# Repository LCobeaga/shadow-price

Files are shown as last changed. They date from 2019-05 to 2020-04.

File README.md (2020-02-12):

Shadow Price
=====

###### Shadow Price is the culmination of many years of CADing, which I had to learn along the way, and Coding, most of which I was taught by @mochoy. It uses brushless motors for the flywheels, a solenoid pusher, and has an integrated IR beam based ammo counter. The shell is based off of the stock weapon model for an auto rifle in the video game Destiny, and my personal blaster is painted like Shadow Price. 

### The STLs for all components are not inhenretly in the correct priting orientation, however there are large flat areas on all parts so use your best judgement when printing and print on these faces

### All minor changes to this document will be dated and placed at the bottom, major changes will be noted at the top here

### Note: This version uses tighter tolerances on all print surfaces. You will likely have to file the removeable components to get them to slide past each other.

## Parts List

For this Blaster you will need:

### Hardware
- 18 Regular Nerf screws (10mm long)
- 10 Small Nerf screws (5mm long)
- two small washers that will not slide over the main screw heads (or switch two of the small screws for something like the washer screws that are used on Stryfe mag releases)
- A small extension spring for the trigger
- A small compression spring for the magazine release (pen spring works)
- Optional: 
  - An 8-32 or M5 machine screw and nut (to hold up butt plate)

### Ammo Counter Electronics
- An Arduino Pro Mini 5V/16MHz 
- A small solderable breadboard
- two .56" 7 segment displays 
- two resistors (based on the color of your display) 
- two 7 segment decoders (make sure they are the same type as your displays)
- two 5mm breadboard compatible momentary push buttons
- A 3mm [IR break beam](https://www.adafruit.com/product/2167)
- A small [limit switch](https://www.allelectronics.com/item/sms-371/spdt-mini-snap-action-switch-w/sim-roller-lever/1.html)
- 22 gauge wire
- Heat shrink 
- Optional: 
  - Multiple colors of wire (to differentiate each button)
  - Bread board jumpers (for creating protoboard)
  - Crimp connectors (for power and ground from ESC-BEC)

__Firing System Electronics__
- An Arduino Pro Mini 5v/16MHz 
- A 10K Ohm [potentiometer](https://www.amazon.com/PoiLee-Potentiometer-Linear-WH148-Shaft/dp/B07BW8JBC8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)
- A medium sized [limit switch](https://www.allelectronics.com/item/sms-219/spdt-mini-snap-action-switch-w/roller-lever/1.html)
- A male battery connector of your prefrence 
- Two ESCs with BEC that are rated up to 3s and have a high enough amperage for your motors
- Two 2204-2300Kv brushless motors (currently working on adding support for 1806 sized motors as well)
- A 35mm stroke 12v electric solenoid 
- A 1N540x Rectifier Diode 
- A IRLB3034PBF MOSFET 
- A 10K Ohm resistor 
- 22 gauge wire
- 16 gauge wire
- heat shrink 
- Optional: 
  - 5mm bullet connectors (for removeable ESCs and easy polarity switching)
  - Crimp connectors (for power from ESC-BEC and to keep small control cables organized)
  - Suild's [MOSFET board 2](https://suild.com/shop/0) (as a replacement for all the MOSFET components)
  
## Software

### Firing Code

To Start, you will need to download the [JC Button Library](https://github.com/JChristensen/JC_Button) by Jack Christensen. 
If you dont know how to download a library to your Arduino IDE [this is a good guide](https://www.digikey.com/en/maker/blogs/2018/how-to-install-arduino-libraries) that I used, just scroll about half way down and there are two mehtods to download the library. 
There are only two areas in the code you should ever realistically need to change, the pinout and revSequence. 
The pinout is simple:
```
#define TRIGGER_PIN 9
#define MOTOR_PIN 10
#define ACTUATOR_PIN 11
#define POT_PIN 1
#define FIRE_MODE_PIN 7
```
- TRIGGER_PIN is for the trigger microswitch.
- MOTOR_PIN is for ***both*** of the signal wires from the ESCs, so make sure you splice the wires together at some point.
- ACTUATOR_PIN is for the signal wire coming off the solenoid MOSFET, in the case of the MOSFET board 2 from Suild it would be a wire coming off the gate pin.
- POT_PIN is for the 10K Ohm potentiometer signal pin, the wire that comes from the middle tab.
- FIRE_MODE_PIN is for an unutilized two position switch that would change between full auto and three round burst. While the code is written for this, there is no mounting geometry in the 3D prints, so you would have to download the .step file in the prints folder and model it in yourself.

The other area of code you might need to change is:
```
void revSequence(){
  flywheelESC.writeMicroseconds(1860);                
  delay(map(analogRead(POT_PIN), 0, 1023, 150, 50));    
  flywheelESC.writeMicroseconds(map(map(analogRead(POT_PIN), 0, 1023, 0, 100), 0, 100, 1250, 1650));
  delay(70);
}
```
In this function you might have to change the delays based on your motors' spin up time. In the first delay, the only values you might need to change are the 150 and 50, which determine how long you need the motors to accelerate for. 
Effectively, the motors accelerate the greatest when an immediate command to full speed is sent. 
What this line of code is doing is using that concept to put the motors at max acceleration for longer when the potentiometer is set to a low speed and accelerate for less time when at the optimal speed. 
Without this line of code the spin up times for all motor speeds would be significantly greater, so change these values only if your first dart fires significantly harder than the rest of your darts when holding the trigger.

The second delay at the end of the function is less complicated, and the only value you might need to change is the 70. 
Once the motor has been told the desired speed (from the previous line of code) it needs a moment to reach it, so the delay is just waiting for the motor to reach that speed, so if your blaster constantly jams when firing the first shot increase this delay, and if you feel like the first dart takes an eternity to fire decrease the delay. 
If you are going to play with this number I suggest you increase or degrease by units of 5 until you reach the minimum delay where your blaster wont jam. 

If you use a different ESC than the 12A AFRO that I use, the min and max speed in microseconds (1860) might be different, and since you will use different motors than the 2204-2300KV Turnigy Multistar Elites (because they are discontinued) the minimum firing and optimal speeds in microseconds (1250 & 1650) will be different. 

To find the max and min speeds in microseconds you will have to refer to the instruction manual that is associated with your ESC, or just test values until you find the threshold value where the motors begin to spin (the minimum microseconds) and find the threshold value where the motor speed does not seem to contimue to increase. 
Once you find these values just ctrl+F in the arduino IDE and switch out every 1060 & 1064 for your new minimum value and switch out every 1860 & 1864 for yor new maximum value (including in the setup code). 
Make sure all of these test you conduct inside the assembled blaster, since it is dependent on the solenoid firing 

To find the minimum firing and optimal speeds you will have to rely solely on testing. 
For minimum firing value, increase from the minimum value in incriments of 10 until you can fire 10 shots full auto without jamming. 
For optimal value, degrease from max in incriments of 10 until the FPS of the dart begins to drop, and you'll need a chronograph for this test (or just look at range with measuring tape, but that will take longer and require more walking). 
These tests can be conducted outside of the blaster, with you manually feeding the darts into the flywheel cage, but it's better if you conduct them inside the blaster since the results will be more realistic. 

### Ammo Counter Code

I will preface this section by saying that this ammo counter is not exlusive to Shadow Price, if you can find some other low current 5v power source to plug it into it will work completely independent. 
The amount it can count up to is also expandable, so if you want to make an ammo counter for your backpack fed blaster feel free to use this design, good luck with counting how many balls you put in at the beginning though. 

Just like before the pinout is relatively simple
```
#define DIG_ONE_A 2
#define DIG_ONE_B 3
#define DIG_ONE_C 4
#define DIG_ONE_D 5
#define DIG_TWO_A 6
#define DIG_TWO_B 7
#define DIG_TWO_C 8
#define DIG_TWO_D 9

#define IR_BEAM 14
#define MAG_SIZE_UP 10
#define MAG_SIZE_DOWN 11
#define MAG_SENSOR 12
```
- DIG_ONE_A-B and DIG_TWO_A-B are the A-B signal pins on the 7 segment decoders, ONE and TWO being for the tens and ones digits, respectively. 
- IR_BEAM is for the signal pin of the IR break beam sensor. 
- MAG_SIZE_UP is for the button that increases the magazine value. 
- MAG_SIZE_DOWN is for the button that decreases the magazine value. 
- MAG_SENSOR is for the limit switch that goes inside the magazine well. 

If you are using this ammo counter for Shadow Price or any other under-100-dart-capacity blaster the only other variables you might change are:
```
int BASEmag  = 17;
int MAXmag   = 35;
```
- BASEmag is the value the ammo counter will show on boot up.
You'll be able to change this value using the up and down buttons, so it doesn't really matter what this value is as long as it's less than the MAXmag value; I like putting it as the capacity of my first magazine in my loadout. 
- MAXmag is the greatest value the ammo counter will display, and the value at which it switches back to 0 if you keep hitting the MAG_SIZE_UP button. 
Make this value the capacity of your largest magazine you would put into the blaster; In my case the largest magazine I own is the 35 round drum. 

Now, if you want to expand this ammo counter to three digits (999 rounds max) or four digits (9999 rounds max) its pretty simple. 
1. Repeat the code in ```void func()``` that displays the ones position for every added digit (I suggest you put it at the end of the function to keep the code organized). 
2. Replace the variable in the ```digitalWrite();``` on your repeated section with the new pinout for your extra digit(s). 
3. Replace the conditions in the DIG_ONE display code with your new highest values (e.g. replace the 10,20,30, etc. with 100,200,300, etc)
4. In decending order, update the conditions for the new digits (e.g. replace the %10 == 1,2,3 etc with %100 == 10,20,30 for digit two, and then leave the conditions alone for the last digit). 
5. Update the BASEmag and MAXmag to values that better reflect your new ammo capacity.

If this didnt make sense feel free ask via reddit (u/Band3rsnach) and I can help, but none of this last bit is required for Shadow Price. 

## Printing and Assembly

### Recomended Printing Orientation

To save time in generating these images I've placed multiple parts on a single print bed. 
I am NOT suggesting you print multiple parts at once unless you are confident in your printer's ability. 
As a general rule, internal features will not need any support, and external features will require supports (if you want the blaster to look pretty). 
A few parts (tail, stock panel left, trigger well left) have extrememly thin surfaces that are for bridging or to reduce supports. 
If you are confident in your printer's ability to bridge use them, if not the surfaces should not cause any problems with supports. 

barrel 1

Depicted: 3X Barrel Tip, Barrel Front, Barrel Middle, Barrel End, 2X Key, Lock

barrel 3

Depicted: Battery Tray

body 1

Depicted: Handle, Knuckle Duster, Left & Right Grill, Bottom Dovetail, Pusher Cover, Solenoid Cover, Top Dovetail, Trigger

body 2

Depicted: Solenoid Mount, Tail, Tail Dovetail, Trigger Well Left & Right

The thin surface circled in red on Trigger Well Left is a built in support, and the Tail has a thin surface for bridging inside it. 

functional

Depicted: Flywheel Smooth, High Crush Flywheel Cage

magwell 1

Depicted : Alignment Bar, Archway, Battery Tray Latch, Bottom Dovetail, Cage Mount, Flywheel Cover, Mag Release Lever, Mag Tooth, Magazine Release, Picatiny Left & Right, Top Dovetail

magwell 2

Depicted: Magwell, Insert

stock

Depicted: 2X Button, 4X Slot, Button Mount, Buttstock, Fin, Left & Right Panel, Stock Main

The part circled in red is the Left Panel, and uses a thin surface for bridging in two areas near each button. 

### Assembly

Now, if like me you are impatient and like to assmeble as you print, I suggest you begin by printing all the parts in the Body and Magwell folders. 
These two folders will make up about 60-70% of your time building Shadow Price since they have a relatively complex assembly that keeps the blaster robust and secure. 
I **highly** suggest you use some form of solvent weld for this blaster instead of an epoxy or superglue, as there are some areas that can take a lot of stress during a fall, and its better to be too secure rather than not. 
For PLA I suggest Weldon 16, for PetG or similar Pet filaments I suggest Weldon 3 or 4 (4 is just more viscous, same formula), and for ABS obviously any form of acetone.
> One cool thing with Weldon 3 or 4 is that it also bonds styrene plastic, so if any part warps (like the Flywheel Cover) you can glue on styrene and it should be super easy to shape and fill gaps. Another good thing about specifically Weldon 3 is it is water thin, so you can use a small spray bottle head (make sure it doesnt disolve in the solvent!) or a brush to cover areas that seem to be cracking. This bonds the layers together like annealing and will make the area stronger (if you can, do this along the top angle of the Cage Mount). You can probably tell at this point that I printed mine in PetG. 

Ok, suggestions over, lets start assembling:

1. Screw into place and glue down Tail Dovetail into tail
step -1

2. Screw into place and glue Insert into Cage Mount

step -2

3. Glue the Cage Mount, Archway, Solenoid Mount, and Tail together in a line. We will call this group the "upper reciever"
step 1

4. Glue and snap the Magwell and Battery Tray Latch together by aligning the circular cutout and snapping in the triangular piece. If you are using a water thin solvent snap the parts together then put a bit of solvent in between the parts.
step 2

5. Glue the Alignment Tab into the Magwell. It should be a tight fit.
step 3

6. Place the Mag Release lever into the Mag tooth and slot both into the back of the Magwell. Make sure the the cutout part of the lever faces away from the magwell, the part of the tooth that sticks out is towards the bottom of the magwell, and that **no glue** gets on any of these parts. 
step 4
step 4-2

These next two steps need to be done pretty quickly if you are not using a water thin solvent, so prepare everything before hand. 
If you are using a water thin solvent, just dont put any solvent in until after all the pieces are locked in place. 

7. Glue and slot Trigger Well Right into the back of the Magwell. This will lock in the magazine lever and tooth so it is critical you align those before gluing this piece on. This collection of pieces we will call the "lower reciever".
step 5

8. Glue, slot, and screw the upper and lower reciever together. Make sure the Alignment Tab is pushed into the back and top of the slot in the Archway, the spike on the front of the Cage Mount is flush with the cut out in the Battery Tray Latch and the screw is in place, the L shaped extrusion is in the corner of the Trigger Well Right, and that the entire top surface of the lower reciever is flush with the bottom of the upper.
step 6

From here on the rest of the parts are mostly cosmetic, however they make up a lot of the length and weight of the blaster.
Make sure they are securely glued and mounted in place or you might get cracks in the shell after painting.

9. Glue and slot the Handle into the bottom of the Trigger Well Right. It should be a secure fit, just make sure you push it as far up as possible. 
step 7

10. Place the small extension spring on to the Magazine Release pin, and insert the pair into the Knuckle Duster. Make sure the spring sits flat on the inside of the Knuckle Duster. I also suggest you paint this component before you put it in since there is no way to get it out. (Optional: add a bit of craft foam to the front of the Magazine Release to make it more comfortable to hit with your middle finger)
step 8

11. Slot the Knuckle Duster assembly into the bottom of the Trigger Well Right and the bottom of the Handle, and align the Magazine Release with the Mag Release Lever, making sure that the system is free to move.
step 9

12. Screw the Knuckle Duster into the bottom of the Handle and glue the top of it into the bottom of the Trigger Well Right and the Magwell. Be careful not to get glue on the release system. 
step 10

13. Glue and slot the Stock onto the back of the Tail. Be sure to get good adhesion both inside and on the two flush surfaces. 
step 11

14. Glue and slot the four Slots into the back of the Stock. Be sure to press them in firmly or the buttplate might be wobbly.
step 12

15. Glue and slot the Right Panel onto the right side of the Stock. Make sure to get good adhesion between the front of the panel and the Tail.
step 13

16. Moving back to the front of the blaster, glue and slot the Top & Bottom Dovetails to the Cage Mount and Battery Tray Latch. Make sure they are flush with the exterior of the blaster. 
step 14

17. Glue and slot Barrel Middle and Barrel Back into place 

step 14b

18. Glue, Slot, and Screw the Barrel assembly into place. 
Make sure it is flush against the Cage Mount both in the front and on the sides.
step 15

The next two steps are for one of the removeable covers, make sure not to glue it into the rest of the blaster.

19. Glue and slot the top and bottom dovetails into the Solenoid Cover
step 17

20. Glue and slot the Trigger Well Left into the bottom of the Solenoid cover. (Optional: glue the two at a slight inward angle so that when screwing into the blaster the panel will always fill the break at the top)
step 18

21. Screw Picatiny Left & Right into the Flywheel Cover and Cage Mount, respectively.
step 19a
step 19b

22. Slot and Glue Grill left & right into the solenoid panel assembly and Solenoid Mount, respectively.
step 20a
step 20b

23. Slot and Glue the three Barrel Tips together.
step 21

Now other than removeable components (Which are screw in) the blaster is fully assembled. 
I suggest that you dont glue the barrel tip assembly into the Barrrel End because its prone to breaking, and make sure that at no point do you glue the Flywheel Cover, Barrel Front, Buttstock, and the Solenoid Cover/Trigger Well Right assembly to the rest of the blaster or you will be unable to insert the internals. 

## Wiring

The blaster can be broken up into two circuits controlled by each of the Arduino Pro Minis and powered by each BEC output. 

This is the diagram for the ammo counter
Ammo_Counter

And this for the firing system
Firing_System

# Updates 

## 10/15/19
2Xkey file was added into the barrel folder. Two of them should be printed along the longest dimention and glued together. Will requre a little less sanding than the regular key, but it will still be a tight fit.

Swapped Left Panel and Stock Main in the stock folder for new versions that make use of a screw and bridging characteristics. No changes to printing orientation. Added another screw in the parts list.

## 10/16/19
Made changes to a majority of body components to improve aesthetics and to remove remnant geometry from older versions. 

Major changes include a block to better attach the Handle to the Trigger Well Right, combining the Solenoid Mount and Top Picatiny to prevent cracking in both parts (as observed in my personal print), and adding a 1 deg angle to the connection between the Trigger Well Left and Solenoid Cover to close shell gaps.

Began to strenghten area around mag release by increasing contact between the Magwell and Knuckle Duster, however no changes have been made to the Magwell so currently the blaster is non printable. 

Updated printing orientation photos and removed assembly step 16 pertaining to the Top Picatiny. 

## 11/24/19
Broke down Barrel Main into two components, Barrel Back and Barrel Middle.

Replaced Barrel end with Barrel Front, now with the new attachment lugs and optimised for bridging. 

## 11/25/19
Filled in gaps between Tail, Solenoid Mount, Solenoid Cover, Trigger Well Right, Magwell, Cage Mount, Flywheel Cover and Archway.

Cut out space in Magwell for the new Knuckle duster, now making the blaster printable again. 

Cut a hole in the top of Cage Mount.

- Created two new parts, Tail Dovetail and Insert.
- Tail Dovetial holds Solenoid Cover from the back and hopefully reduce flexing on Solenoid Mount.
- Insert goes inside of Cage Mount and will hopefully reduce the cracking that occurs in that area.
- Parts list updated to reflect four screws that hold the pieces in place.

## 11/26/19
Increased Insert tolerances. 

Added fillets to the picatiny on Solenoid Mount to reduce the need for supports.

Updated printing and assembly photos to reflect geometry changes. 

NOTE: Since many changes had no effect on assembly, not all photos were switched out, so go by description and use the photos as refrence. 

## 12/11/19
Multiple minor geometry changes as I print another shadow price and issues arise. 

- Pushed back dovetail and increased angle on Handle.
- New female side of dovetail on Trigger Well Left.
- Added screwport between Trigger Well Right and Left.
- Added reinfocement bar to Solenoid Cover to prevent cracking on small upper area.
- Removed extraneous walls in Archway to help with aethetics.
- Minor wall adjustments on Solenoid Mount so it meshes better with Archway and requires less support.

Updated Parts list with extra screw.

## 12/14/19
Redesigned all dovetails connecting the removeable handle cover from the blaster.

- Added new part, Tail Decoration, to prevent the need for a large support tower.
- Added a Dovetail to the side and back of Magwell and Archway. 
- New locations for two of the screws, moved from Trigger Well Left onto Solenoid Cover.
- Removed Top and Bottom Dovetails as they are now extraneous parts.

Created new set of combined parts for larger printers (150mm+ in X or Y).

- Added new parts Trigger Well Left Combined, Trigger Well Right Combined, Handle Combined.
- Moved geometry constraining the magazine release system onto the trigger well pair, should now allow for removeable components.

No changes to assembly order but some steps need to be removed due to dovetail changes.

## 12/16/19
Reinforced Magwell and surrounding parts

 - Added bridge support to Magwell dovetail.
 - Thickened wall on Magwell under the cage.
 - Made the anchor for Battery Tray Latch larger.
 - Removed extra features on inside of Cage Mount, added chamfers to reduce supports and increase strength, added extra screwport at the top of the Back Barrel connection, thickened walls and added bridge supports. 

Minor changes to Solenoid Mount and Cover to reduce required support.

Removed the original trigger well files as the new dovetail geometry was not reflected in their design and made them redundant.
The Knuckle Duster does not reflect the changes on the Trigger Well Combined files, so for now only use Handle Combined.

Cleaned up extraneous surfaces on stock main.

## 2/12/20
Dropped height of Battery Tray so top is planar, makes printing easier.

Increased wall length of Barrel Middle and Front to match Battery Tray.

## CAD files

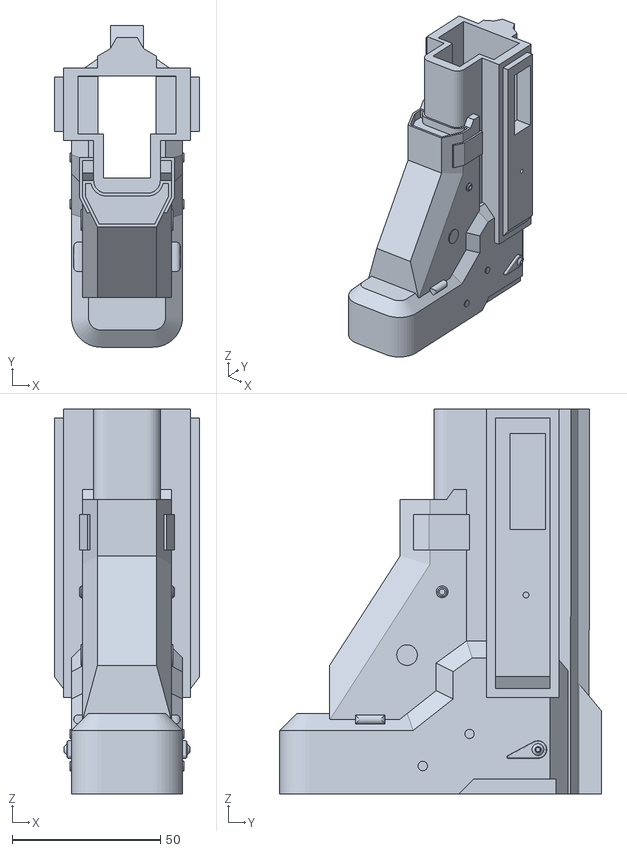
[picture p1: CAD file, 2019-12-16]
prints/stock/stock main.stl
49.0 x 108.6 x 130.0

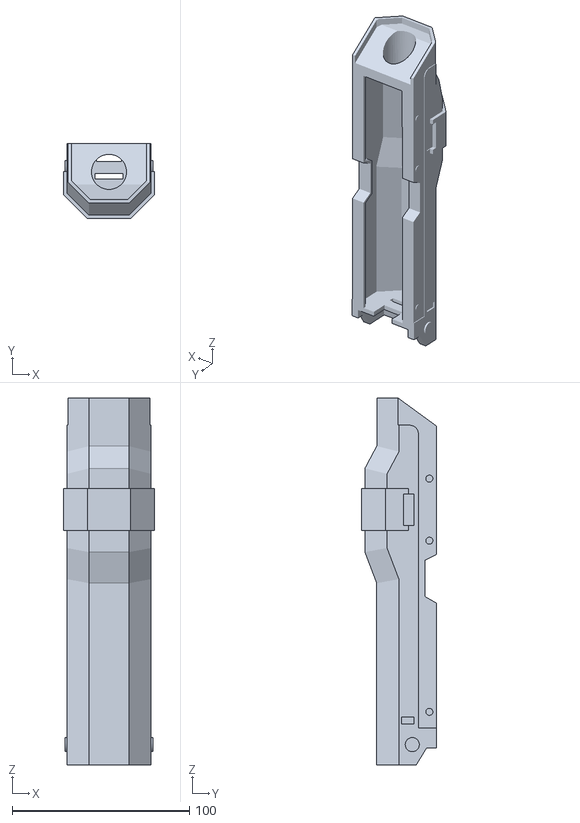
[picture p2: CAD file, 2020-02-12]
prints/barrel/battery tray.stl
51.5 x 42.5 x 206.9

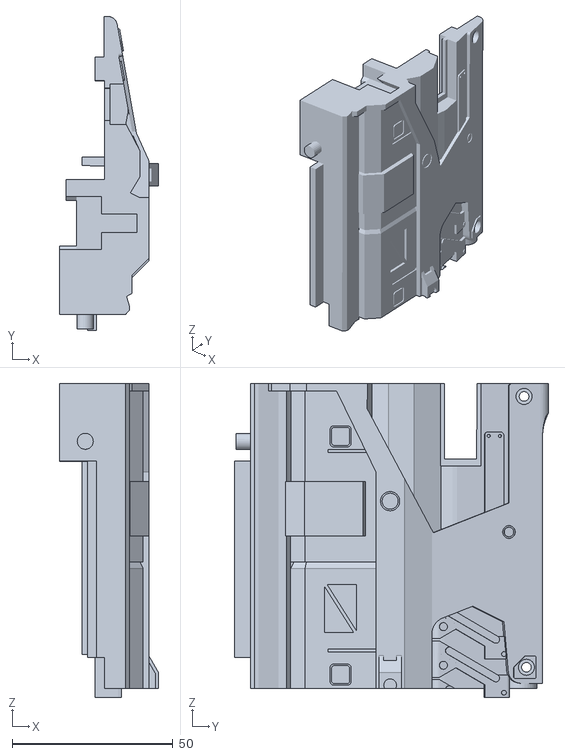
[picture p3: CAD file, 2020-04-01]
prints/body/solenoid cover.stl
30.8 x 97.6 x 97.6

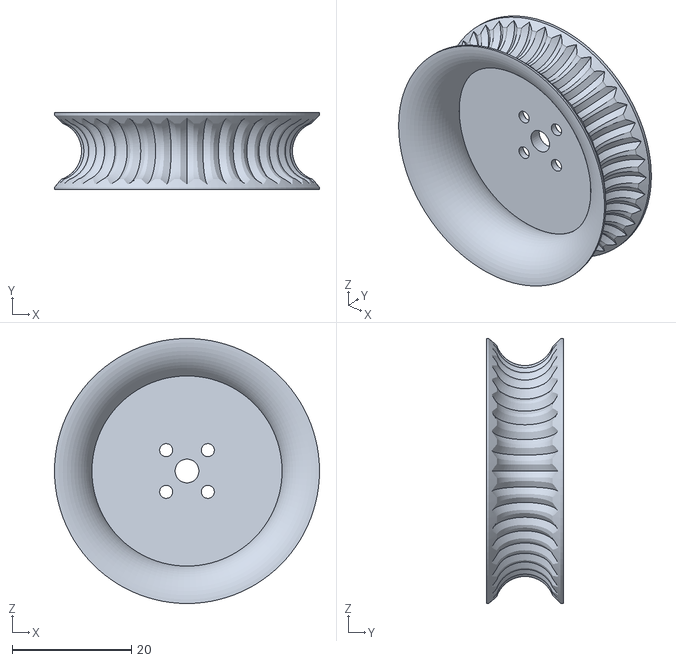
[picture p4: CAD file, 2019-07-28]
prints/functional/current/flywheel vertical lines.stl
44.5 x 13.0 x 44.5

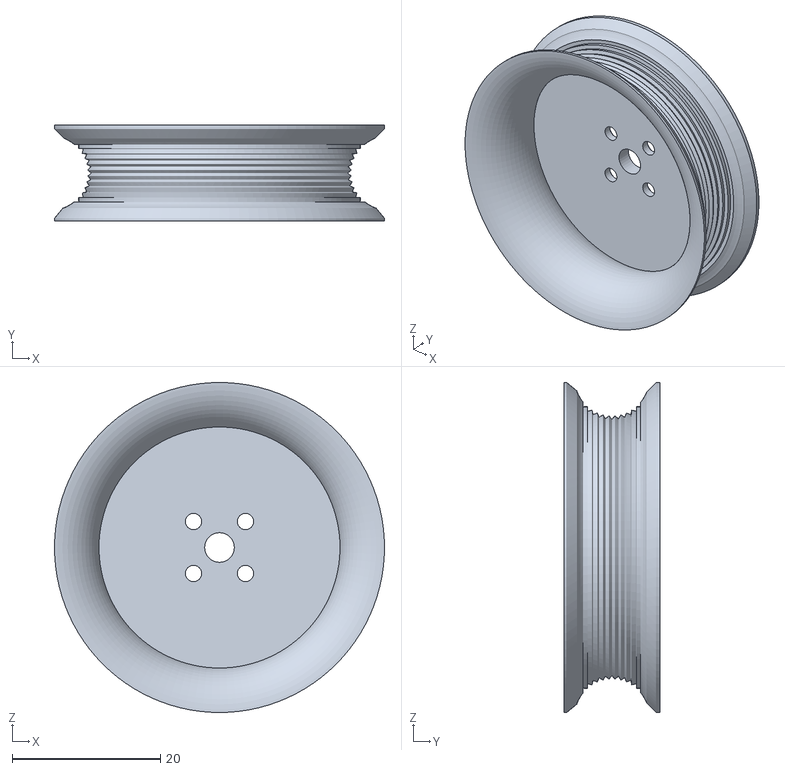
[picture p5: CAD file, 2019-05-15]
prints/functional/flywheel lateral lines deep.stl
44.5 x 13.0 x 44.5

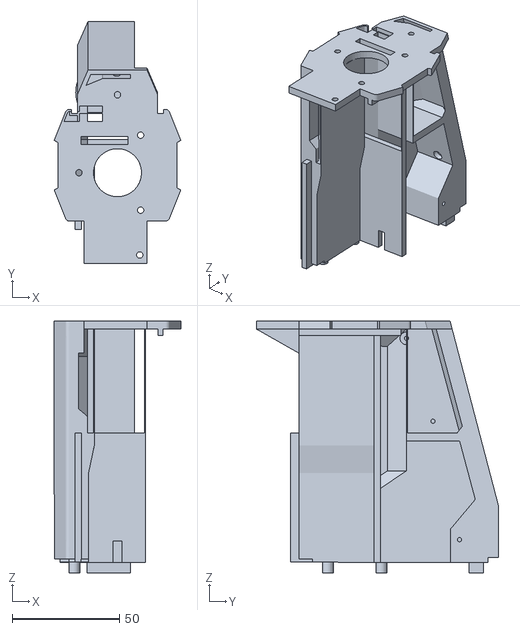
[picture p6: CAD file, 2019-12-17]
prints/magwell/cage mount.stl
59.1 x 113.0 x 117.6

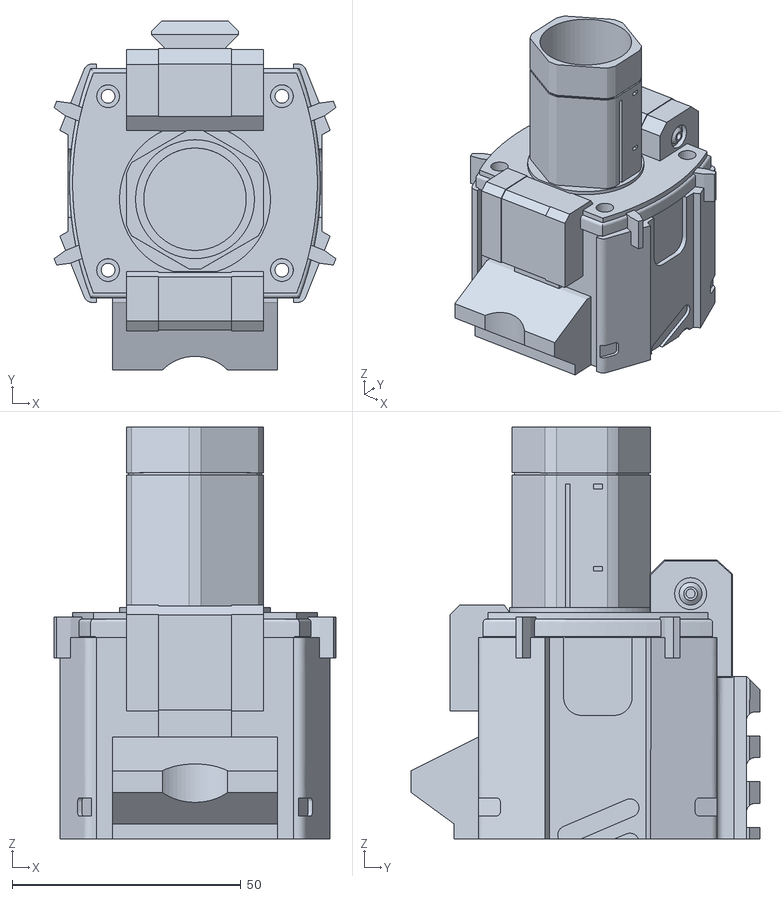
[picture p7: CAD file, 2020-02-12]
prints/barrel/barrel front.stl
61.6 x 76.3 x 90.1

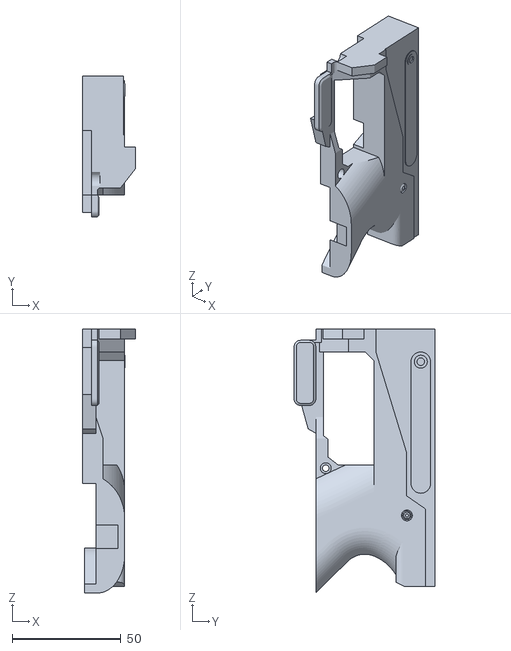
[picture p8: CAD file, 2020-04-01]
prints/body/trigger well left combined.stl
24.5 x 64.8 x 121.4

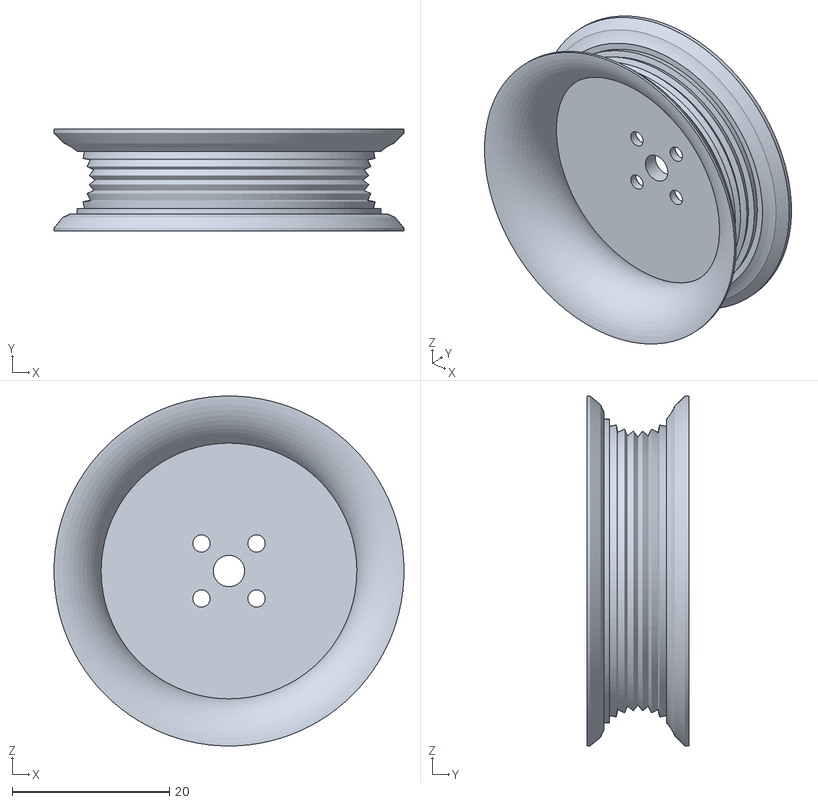
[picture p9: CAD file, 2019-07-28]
prints/functional/current/flywheel lateral lines.stl
44.5 x 13.0 x 44.5

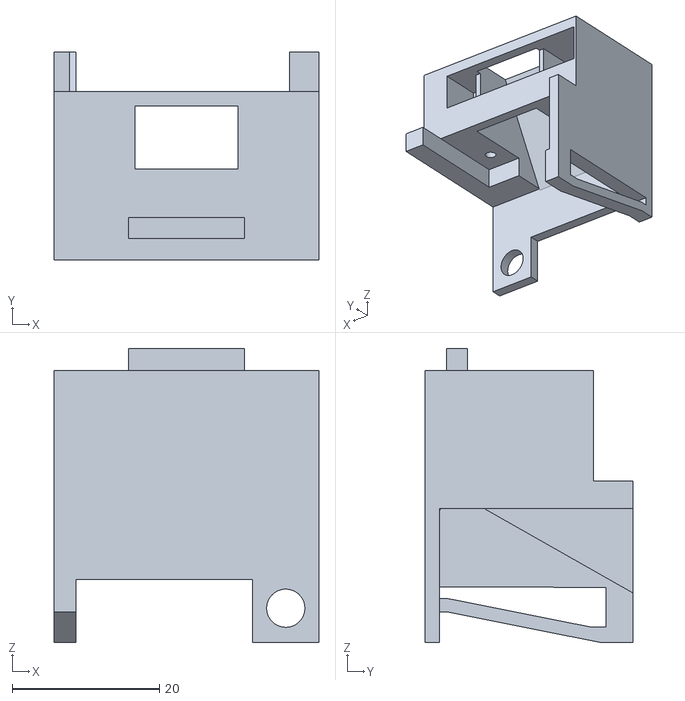
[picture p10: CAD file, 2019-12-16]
prints/magwell/batery tray latch.stl
36.0 x 28.3 x 40.0

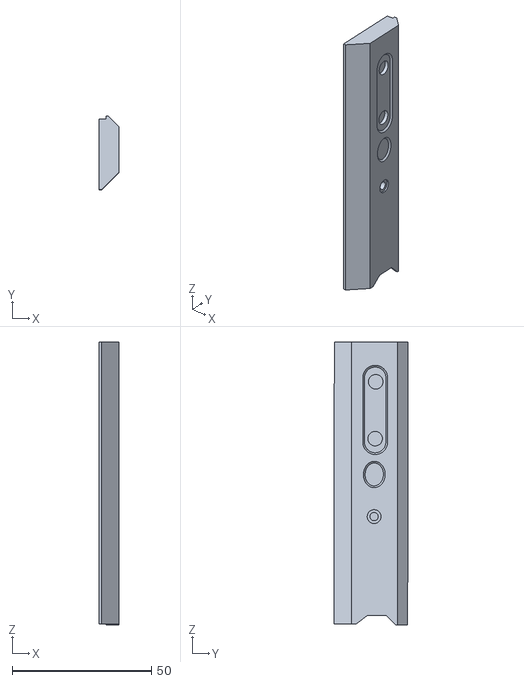
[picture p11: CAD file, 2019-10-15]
prints/stock/left panel.stl
7.25 x 26.5 x 101.8

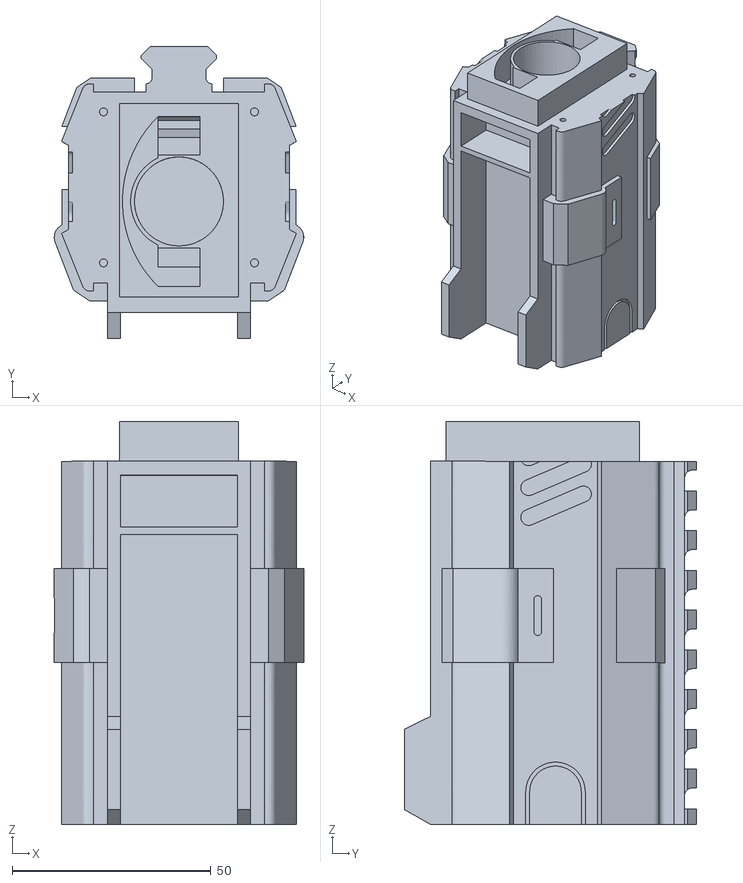
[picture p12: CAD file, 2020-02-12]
prints/barrel/barrel middle.stl
62.8 x 73.5 x 101.4

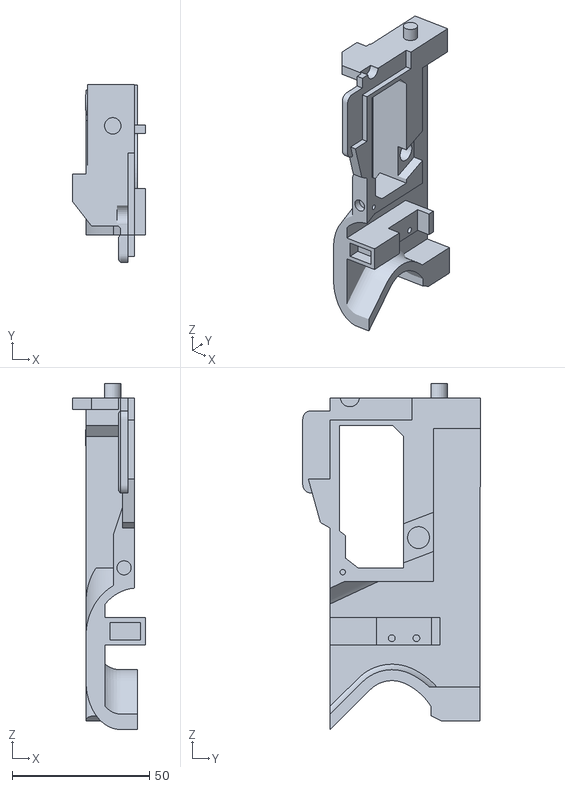
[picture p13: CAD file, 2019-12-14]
prints/body/trigger well right combined.stl
26.8 x 64.8 x 126.2

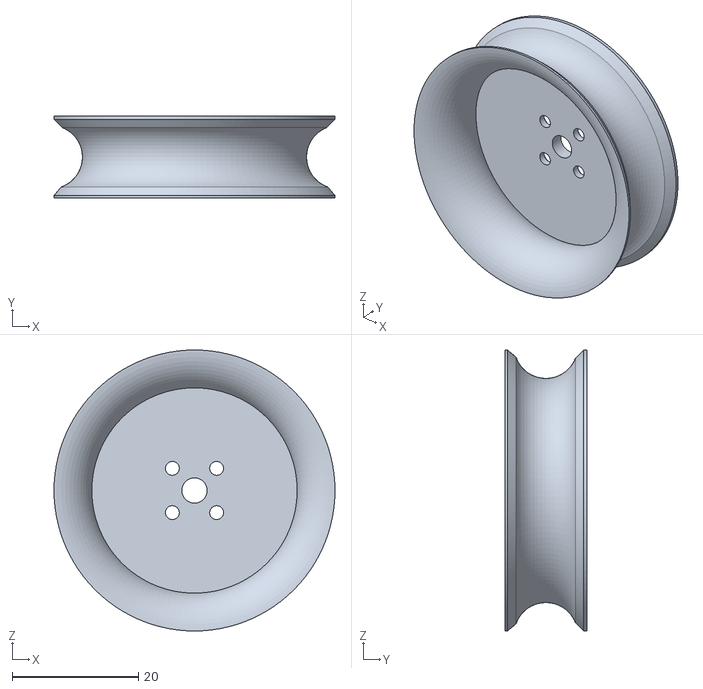
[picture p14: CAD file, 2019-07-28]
prints/functional/current/flywheel smooth.stl
44.5 x 13.0 x 44.5

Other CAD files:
prints/functional/flywheel vertical lines.stl
prints/functional/flywheel cage.stl
prints/magwell/archway.stl
prints/stock/fin.stl
prints/barrel/2Xkey.stl
prints/barrel/3Xbarrel tip.stl
prints/barrel/barrel back.stl
prints/barrel/key.stl
prints/barrel/lock.stl
prints/body/Tail Decoration.stl
prints/body/handle combined.stl
prints/body/handle.stl
prints/body/knuckle duster.stl
prints/body/left grill.stl
prints/body/pusher cover.stl
prints/body/right grill.stl
prints/body/solenoid mount.stl
prints/body/tail dovetail.stl
prints/body/tail.stl
prints/body/trigger.stl
prints/functional/cage v1.stl
prints/functional/cage v2.stl
prints/functional/cage v3.stl
prints/functional/current/flywheel cage hi crush canted.stl
prints/functional/current/flywheel cage hi crush.stl
prints/functional/current/flywheel lateral lines deep.stl
prints/functional/flywheel lateral lines.stl
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

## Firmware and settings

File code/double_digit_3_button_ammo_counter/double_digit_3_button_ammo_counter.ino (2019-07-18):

/*
Luca Cobeaga (u/Band3rsnach) 

Ammo Counter Code


last updated 07/18/19


i tried to add comments to all code because im bad at this stuff, so if you are confused look at what i wrote to clear up confusion, or direct message me 
with any questions you cant find the answer too



this code is simple because i am NOT multiplexing the two 7 segment displays, and im using decoders to make my 10 pins off the 7 segment into 4 
thus this ammo counter has some specific hardware limit:

1. you MUST be using either TWO SEPARATE 7 segment displays or a double digit display that has 18 TOTAL pins. the two digits are controlled SEPARATELY
2. you MUST be using decoders that match your 7 segment displays, they are categorized by either common anode or common cathode. 
3. this code is designed for common anode(common positive pin), if you have something different you just need to update the HIGH and LOW sets at the 
   bottom of this code to make numbers, and plug the common into Vcc for common anode or Gnd for common cathode


Definitions:

MAXmag - Maximum Magazine capacity, as in the largest magazine you own that will be shot with this ammo counter (mine is a 35 dart drum, so my MAXmag is 35)

BASEmag - BASE magazine size, as in the value that is displayed the moment the ammo counter is turned on (this doesn't really matter since you can change 
          this value at any moment and the code will remember the new value) 



oh and to note, this counter only supports up to 99 rounds in a magazine, if you want to go up to 999 (for like a proton pack or something) you need to add another digit
and another decoder, and add a digthree A through D
*/

//next 9 are names of the pinouts of the outbound signals (code applies voltages), so change based on where you plugged things in
//digits are from right to left, or digit one is the tens and digit two is the ones

#define DIG_ONE_A 2
#define DIG_ONE_B 3
#define DIG_ONE_C 4
#define DIG_ONE_D 5
#define DIG_TWO_A 6
#define DIG_TWO_B 7
#define DIG_TWO_C 8
#define DIG_TWO_D 9

//these are also named pins, but of inbound signals (code is checking for voltages), change based on where you plugged things in

#define IR_BEAM 14
#define MAG_SIZE_UP 10
#define MAG_SIZE_DOWN 11
#define MAG_SENSOR 12

//this variable is what we paste the IR beam results to, all it does is simplify writing, dont change 

int sensorState = 0;

//these are just variables I mentioned, change based on what I said above 

int BASEmag  = 17;
int MAXmag   = 35;
int CURRENTmag;

void setup() {

//this is just telling the code what each pin does, so all the variables above are called upon down here
//think like algebra 2 where you plug in the value for the variable
  
pinMode(DIG_ONE_A,OUTPUT);
pinMode(DIG_ONE_B,OUTPUT);
pinMode(DIG_ONE_C,OUTPUT);
pinMode(DIG_ONE_D,OUTPUT);
pinMode(DIG_TWO_A,OUTPUT);
pinMode(DIG_TWO_B,OUTPUT);
pinMode(DIG_TWO_C,OUTPUT);
pinMode(DIG_TWO_D,OUTPUT);
pinMode(MAG_SIZE_UP,INPUT_PULLUP);        //for all 3 im turning on an internal resistor so when it sees the voltage pass through it doesnt burn the chip
pinMode(MAG_SIZE_DOWN,INPUT_PULLUP);
pinMode(MAG_SENSOR,INPUT_PULLUP);
pinMode(IR_BEAM,INPUT);

digitalWrite(IR_BEAM, HIGH);    //turns on ir beam light
}

void loop() {
  sensorState = digitalRead(IR_BEAM);                //sets output of IR_BEAM to the variable sensorstate
  func(CURRENTmag);                                 //func is all the binary for the decoders saved and CURRENTmag is the CURRENT magazine size
  
  while(!digitalRead(MAG_SENSOR)==HIGH){       //this keeps code within this loop until statement is true
    buttonValue();                                  //the function that allows the up and down buttons to change BASE magazine size
    func(BASEmag);                                  //displays the BASE magazine size 
    CURRENTmag=BASEmag;                             //sets the CURRENT magazine size to the BASE magazine size
  }
  
  if(digitalRead(MAG_SENSOR)==HIGH && !sensorState==HIGH){        //checks if the magazine is inserted AND if a dart passed the sensor
  CURRENTmag--;                                                //makes the CURRENT magazine size decrease by 1
  delay(70);                                                  //debounce, if this wasnt here some darts could actaully set off the breakbeam twice 
  }
}

void buttonValue(){                    //the function that allows the up and down buttons to change the BASE magazine size
  if(digitalRead(MAG_SIZE_UP)==LOW){    //looks to see if you are pressing the up button
    delay(200);                        //debounce
    if (BASEmag<MAXmag){               //checks to see if the BASE magazine size is less than 35, if you have larger magazine size you change this and add code below
    BASEmag = ++BASEmag;               //increases BASE magazine size by 1
    }
    else {                             //pretty much just cycles back around so if a button breaks you can still change your BASE magazine size
      BASEmag = 0;                     //if you reach a value greater than maximum magazine size it cycles back to 0
    }
  }
  if(digitalRead(MAG_SIZE_DOWN)==LOW){   //looks to see if you are pressing the down button
    delay(200);                         //debugger
    if(BASEmag>0){                      //looks to see if BASE magazine size is greater than 0
      BASEmag = --BASEmag;              //decrease BASE magazine size by 1
    }
    else{                               //pretty much just cycles back around so if a button breaks you can still change your BASE magazine size
      BASEmag = MAXmag;                 //if you reach a value lower than 0 you cycle back to maximum magazine size
    }
  }
}
void func(int CURRENTmag){
/*
 
the next few values are for the FIRST digit of the 7 segment, the 10s position 
it works by an else if statement, where the first statement, in order, found to be true is run, and all others are ignored

 */
  if(CURRENTmag<10){
 //zero
  digitalWrite(DIG_ONE_A,LOW);
  digitalWrite(DIG_ONE_B,LOW);
  digitalWrite(DIG_ONE_C,LOW);
  digitalWrite(DIG_ONE_D,LOW);
  }
  else if(CURRENTmag<20){
 //teens
  digitalWrite(DIG_ONE_A,HIGH);
  digitalWrite(DIG_ONE_B,LOW);
  digitalWrite(DIG_ONE_C,LOW);
  digitalWrite(DIG_ONE_D,LOW);
  }
  else if(CURRENTmag<30){
 //twenty
  digitalWrite(DIG_ONE_A,LOW);
  digitalWrite(DIG_ONE_B,HIGH);
  digitalWrite(DIG_ONE_C,LOW);
  digitalWrite(DIG_ONE_D,LOW);
  }
  else if(CURRENTmag<40){
 //thirty
  digitalWrite(DIG_ONE_A,HIGH);
  digitalWrite(DIG_ONE_B,HIGH);
  digitalWrite(DIG_ONE_C,LOW);
  digitalWrite(DIG_ONE_D,LOW);
  }
  else if(CURRENTmag<50){
 //fourty
  digitalWrite(DIG_ONE_A,LOW);
  digitalWrite(DIG_ONE_B,LOW);
  digitalWrite(DIG_ONE_C,HIGH);
  digitalWrite(DIG_ONE_D,LOW);
  }
  else if(CURRENTmag<60){
 //fifty
  digitalWrite(DIG_ONE_A,HIGH);
  digitalWrite(DIG_ONE_B,LOW);
  digitalWrite(DIG_ONE_C,HIGH);
  digitalWrite(DIG_ONE_D,LOW);
  }
  else if(CURRENTmag<70){
 //sixty
  digitalWrite(DIG_ONE_A,LOW);
  digitalWrite(DIG_ONE_B,HIGH);
  digitalWrite(DIG_ONE_C,HIGH);
  digitalWrite(DIG_ONE_D,LOW);
  }
  else if(CURRENTmag<80){
 //seventy
  digitalWrite(DIG_ONE_A,HIGH);
  digitalWrite(DIG_ONE_B,HIGH);
  digitalWrite(DIG_ONE_C,HIGH);
  digitalWrite(DIG_ONE_D,LOW);
  }
  else if(CURRENTmag<90){
 //eighty
  digitalWrite(DIG_ONE_A,LOW);
  digitalWrite(DIG_ONE_B,LOW);
  digitalWrite(DIG_ONE_C,LOW);
  digitalWrite(DIG_ONE_D,HIGH);
  }
  else if(CURRENTmag<100){
 //ninety
  digitalWrite(DIG_ONE_A,HIGH);
  digitalWrite(DIG_ONE_B,LOW);
  digitalWrite(DIG_ONE_C,LOW);
  digitalWrite(DIG_ONE_D,HIGH);
  }
  
/* 
   
the values below are for the SECOND digit of the 7 segment display, it works by using a modulus (the percentage symbol%)
a modulus pretty much divides the first value by the second, and returns the REMAINDER of the division, so 1 % 10 returns 1, 13 % 10 returns 3 and so on

*/
  
  if(CURRENTmag % 10 == 0){
 //zero
  digitalWrite(DIG_TWO_A,LOW);
  digitalWrite(DIG_TWO_B,LOW);
  digitalWrite(DIG_TWO_C,LOW);
  digitalWrite(DIG_TWO_D,LOW);
  }
    if(CURRENTmag % 10 == 1){
  //one
  digitalWrite(DIG_TWO_A,HIGH);
  digitalWrite(DIG_TWO_B,LOW);
  digitalWrite(DIG_TWO_C,LOW);
  digitalWrite(DIG_TWO_D,LOW);
    }
    if(CURRENTmag % 10 == 2){
  //two
  digitalWrite(DIG_TWO_A,LOW);
  digitalWrite(DIG_TWO_B,HIGH);
  digitalWrite(DIG_TWO_C,LOW);
  digitalWrite(DIG_TWO_D,LOW);
    }
    if(CURRENTmag % 10 == 3){
  //three
 digitalWrite(DIG_TWO_A,HIGH);
  digitalWrite(DIG_TWO_B,HIGH);
  digitalWrite(DIG_TWO_C,LOW);
  digitalWrite(DIG_TWO_D,LOW);
    }
    if(CURRENTmag % 10 == 4){
  //four
  digitalWrite(DIG_TWO_A,LOW);
  digitalWrite(DIG_TWO_B,LOW);
  digitalWrite(DIG_TWO_C,HIGH);
  digitalWrite(DIG_TWO_D,LOW);
    }
    if(CURRENTmag % 10 == 5){
  //five
  digitalWrite(DIG_TWO_A,HIGH);
  digitalWrite(DIG_TWO_B,LOW);
  digitalWrite(DIG_TWO_C,HIGH);
  digitalWrite(DIG_TWO_D,LOW);
    }
    if(CURRENTmag % 10 == 6){
  //six
  digitalWrite(DIG_TWO_A,LOW);
  digitalWrite(DIG_TWO_B,HIGH);
  digitalWrite(DIG_TWO_C,HIGH);
  digitalWrite(DIG_TWO_D,LOW);
    }
    if(CURRENTmag % 10 == 7){
  //seven
  digitalWrite(DIG_TWO_A,HIGH);
  digitalWrite(DIG_TWO_B,HIGH);
  digitalWrite(DIG_TWO_C,HIGH);
  digitalWrite(DIG_TWO_D,LOW);
    }
    if(CURRENTmag % 10 == 8){
  //eight
  digitalWrite(DIG_TWO_A,LOW);
  digitalWrite(DIG_TWO_B,LOW);
  digitalWrite(DIG_TWO_C,LOW);
  digitalWrite(DIG_TWO_D,HIGH);
    }
    if(CURRENTmag % 10 == 9){
  //nine
  digitalWrite(DIG_TWO_A,HIGH);
  digitalWrite(DIG_TWO_B,LOW);
  digitalWrite(DIG_TWO_C,LOW);
  digitalWrite(DIG_TWO_D,HIGH);
    }
}

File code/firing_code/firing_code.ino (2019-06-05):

//luca cobeaga, brushless and solenoid flywheel blaster SHADOW PRICE
//last updated 06/05/19
//for the JC_Button.h library go to https://github.com/JChristensen/JC_Button and download to your libraries in arduino IDE
//lucacobeaga@gmail.com for questions

#include <JC_Button.h>   //include code libraries for a button with debounce, effectively its like a cited source, and below im writing the evience i gained from reading it
#include <Servo.h>       //include code libraries for servos, this is PWM and is how we are contrlling the brushless motors

#define TRIGGER_PIN 9      //sets trigger limit switch to pin 9
#define MOTOR_PIN 10       //sets ESC control to pin 10
#define ACTUATOR_PIN 11    //sets solenoid pusher pin to 11
#define POT_PIN 1          //sets poteniometer pin to 1
#define FIRE_MODE_PIN 7    //sets on off switch pin to 7

Servo flywheelESC;                              //create servo object to control the esc 
Button trigger(TRIGGER_PIN, 25, true, true);    //creates trigger button, read button library for syntax
Button selectFire(FIRE_MODE_PIN, 25, true, true);

void setup() {
  flywheelESC.attach(MOTOR_PIN);     //attaches the servo on pin 10 to the servo object
  pinMode(ACTUATOR_PIN,OUTPUT);      //tells the chip to treat the mosfet controlling the solenoid as an outbound signal, as in it doesnt return a signal

  delay(2000);
  flywheelESC.writeMicroseconds(1864);  //runs the ESC startup sequence by giving highest possible speed value
  delay(2000);                          //waits, this is when you hear the three beeps, last two sound the same
  flywheelESC.writeMicroseconds(1064);  //gives lowest possible speed value
  delay(2000);                          //waits to make sure esc took code, here you hear two more beeps, last one very high pitched

  trigger.begin();          //initializes button and connected pin
  selectFire.begin();       //initializes slide switch and connected pin
}                                       

void loop() {
  trigger.read();     //only time the trigger is actually checked
  selectFire.read();
  
  if(selectFire.isPressed()){
    //pulseFire();
    AutoFire();
  }

  AutoFire();
  //pulseFire();

}


void AutoFire() {

  if(trigger.wasPressed()){               //if trigger was previously pressed 

    revSequence();

    while(trigger.isPressed()){
      digitalWrite(ACTUATOR_PIN,HIGH);      //gives a signal to MOSFET to allow current flow (N-channel MOSFETs are like normally closed switches you open with positive current)
      delay(30);                            //wait for solenoid to move out far enough
      digitalWrite(ACTUATOR_PIN,LOW);       //close current flow to solenoid
      delay(70);                           //wait for wheels to get back to speed
      trigger.read();
    } 
  } 

  flywheelESC.writeMicroseconds(1060); //gives lowest tested value where motors move so trigger can be more responsive, but draws more current so you need a big battery
  digitalWrite(ACTUATOR_PIN,LOW);      //also turns off solenoid, can never be too safe (solenoid heats up fast)
}


void pulseFire() {
  if(trigger.wasPressed()){     
    
    revSequence();

    for(int i = 0; i < 3; i++){         //cycle pusher 3 times, if longer or shorter pulse needed change the 3 value
      digitalWrite(ACTUATOR_PIN,HIGH);
      delay(70);
      digitalWrite(ACTUATOR_PIN,LOW);
      delay(90);
    }
  } 

  flywheelESC.writeMicroseconds(1060); 
  digitalWrite(ACTUATOR_PIN,LOW);
}


void revSequence(){
  flywheelESC.writeMicroseconds(1860);                //max speed to get best acceleration
  delay(map(analogRead(POT_PIN), 0, 1023, 150, 50));    //delay inverse to speed to accelerate to below speed
  flywheelESC.writeMicroseconds(map(map(analogRead(POT_PIN), 0, 1023, 0, 100), 0, 100, 1250, 1650));
  delay(70);
}

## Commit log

2018-11-07 Add files via upload
    this is the file for the printed wheels, print with the large flat face down, should need very little support
    [flywheel_lathed.STL]
2018-11-15 Update double_digit_3_button_ammo_counter.ino
    Changed the pins to better suit the arduino for plug in adapters
2018-11-28 Add files via upload
    these wheels should add 2mm of crush to the darts, still 98% envelopment with chamfered edges to reduce likeliness of jamming
    [flywheel_lathed_hi_crush.STL]
2018-11-28 Add files via upload
    3D printed testing cage, canted for possible better accuracy
    [cage v1.stl]
2018-11-30 Add files via upload
    new canted cage that had the correct motor height for a centered dart and screw ports in the right places
    [cage v2.stl]
2018-11-30 Add files via upload
    i forgot to open up the wire channel more to actually fit the three wires
    [cage v3.stl]
2018-12-02 Add files via upload
    This is just a preliminary code for the firing mechanism, using Jack Christensen's button library https://github.com/JChristensen/JC_Button . It functions semi auto and the wheels are constantly running at low velocity to try and counteract the low acceleration I am personally seeing with them, which is an issue I am looking into. Newer versions should add select fire, potentiometer controlled flywheel velocity, and fix the acceleration issues.
    [firing_code.ino]
2018-12-07 moved prints into new folder
    [cage v1.stl, cage v2.stl, cage v3.stl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]
2018-12-07 added support for potentiometer driven motor speed
2018-12-08 variable motor velocity
2019-04-09 test if lateral cuts in wheels help improve performance
    [flywheel lateral lines.stl]
2019-04-09 small gates added to prevent dart catching
    [flywheel cage.stl]
2019-05-15 changed motor position to center flywheels
    [flywheel cage hi crush canted.stl]
2019-05-15 non canted version of original cage
    [flywheel cage hi crush.stl]
2019-05-15 new worker-style wheels, 1mm depth cuts
    [flywheel vertical lines.stl]
2019-05-15 lateral cut wheels with 1mm depth cuts
    at the very center the print gets extremely weak and has broken during testing. will have to either increase wheel root diameter or decrease back wall diameter, both would increase the wall thickness, but not keep mass and root diameter equal to the other wheels
    [flywheel lateral lines deep.stl]
2019-05-15 increased acceleration delay and set max PWM input
    after some testing i found that max dart velocity occurred at a lower motor speed motor max speed, so i updated the max PWM input to reflect those findings. the blaster kept jamming as well so i added delay to the acceleration to assure full speed before dart is pushed in, however it has not helped so i believe the gap between the bottom of the wheel and the cage, along with the wheels being too far up, is to blame for jams when inside the blaster (note: the darts never jam when manually fed outside of the blaster)
    [firing_code.ino]
2019-05-16 revsequence() delays were to blame for jamming
    [firing_code.ino]
2019-06-05 new timings for solenoid as to not squish darts
2019-06-23 changed pin callouts to define from int
2019-06-23 changed pin numbers
2019-07-12 switched Boolean logic to reflect wiring
2019-07-27 full blaster assembly
2019-07-27 front end of the blaster
    [3Xbarrel tip.stl]
2019-07-27 the rest of the barrel files
    [barrel end.stl, battery tray.stl, key.stl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]
2019-07-27 first body component
    [bottom dovetail.stl]
2019-07-27 created body folder
    [bottom dovetail.stl]
2019-07-27 the rest of the body files
    [handle.stl, knuckle duster.stl, left grill.stl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]
2019-07-27 first magwell component
    [alignment bar.stl]
2019-07-27 would not allow me to create new folder
    [alignment bar.stl]
2019-07-27 Rename prints/alignment bar.stl to prints/magwell/alignment bar.stl
    [alignment bar.stl]
2019-07-27 first stock file
    [2Xbutton.stl]
2019-07-27 made stock folder
    [2Xbutton.stl]
2019-07-27 rest of stock folders
    [4Xslot.stl, button mount.stl, buttstock.stl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]
2019-07-28 final version for 1804 size BLDC cage
    [flywheel cage hi crush.stl]
2019-07-28 most recent version of all cages and wheels
    [flywheel cage hi crush canted.stl, flywheel cage hi crush.stl, flywheel lateral lines deep.stl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]
2019-10-02 wrote read me
    will update with firing system schematic soon
2019-10-15 new key for horizontal printing
    if the single piece key breaks often for you (like mine) print a pair of these flat face down and the key should no longer break
    [2Xkey.stl]
2019-10-15 bridging surfaces and screw mount added
2019-10-15 added a screw port for new left panel assembly
    [stock main.stl]
2019-10-17 small changes for improved printing and strength
    [handle.stl, knuckle duster.stl, solenoid cover.stl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]
2019-10-17 integrated into solenoid mount
    [top picatiny.stl]
2019-10-17 fixed surface errors
    [stock main.stl]
2019-11-25 new geometry for smaller prints & less supports
    [barrel back.stl, barrel front.stl, barrel middle.stl]
2019-11-25 obsolete version
    [barrel end.stl]
2019-11-25 placed in tolerances
    [barrel front.stl]
2019-11-25 gap filling and new tail dovetail
    [solenoid cover.stl, solenoid mount.stl, tail dovetail.stl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]
2019-11-26 gap filling
    [archway.stl, magwell.stl]
2019-11-26 geometry changes to strengthen parts
    [cage mount.stl, insert.stl, magwell.stl]
2019-11-26 tighter tolerances
    [flywheel cover.stl]
2019-11-26 tighter dovetail tolerances
    [magwell.stl]
2019-11-26 better tolerances
    [insert.stl]
2019-12-04 changes of small features to increase visibility
    [solenoid cover.stl, solenoid mount.stl]
2019-12-06 reinforced top
    [solenoid cover.stl]
2019-12-06 removed unnecessary surface behind top dovetail
    [archway.stl]
2019-12-07 changes for better printing
    [archway.stl, magwell.stl]
2019-12-07 new geometry for better printing
    [solenoid mount.stl]
2019-12-11 extra screw port and better dovetail
    [handle.stl, trigger well left.stl, trigger well right.stl]
2019-12-14 New dovetail locations
    [archway.stl, magwell.stl]
2019-12-14 New dovetail and screw locations
    [Tail Decoration.stl, solenoid mount.stl, tail.stl]
2019-12-14 combined components for larger printers
    [handle combined.stl, trigger well left combined.stl, trigger well right combined.stl]
2019-12-14 new dovetail geometry
    [bottom dovetail.stl]
2019-12-16 added extra screw port
    [barrel back.stl]
2019-12-16 bridging geometry and reinforcement of connections
    [archway.stl, batery tray latch.stl, cage mount.stl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]
2019-12-16 optimizing for less supports
    [solenoid cover.stl, trigger well left combined.stl]
2019-12-16 removed extraneous surfaces
    [stock main.stl]
2019-12-17 added chamfer to base of part
    [cage mount.stl]
2019-12-17 replaced by Trigger Well Left Combined
    [trigger well left.stl]
2019-12-17 replaced by Trigger Well Right Combined
    [trigger well right.stl]
2019-12-17 fix to a misaligned screw port
    [barrel back.stl]
2020-02-12 minor geometry changes for better printing
    [barrel front.stl, barrel middle.stl, battery tray.stl]
2020-04-01 changed surfaces for minimized gaps
    [solenoid cover.stl, trigger well left combined.stl]
